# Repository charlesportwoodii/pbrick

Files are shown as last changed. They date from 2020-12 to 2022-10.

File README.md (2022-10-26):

<div align="center">
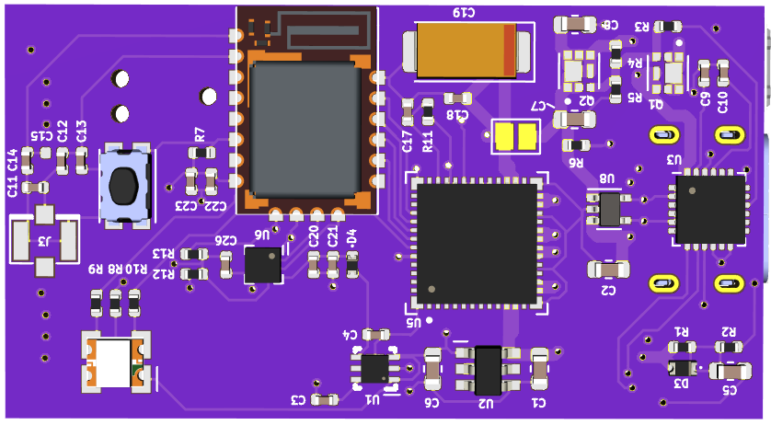
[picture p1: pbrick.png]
  

  <h1>PBRICK</h1>

  <p>
    <strong>A USB-C PD powered, Bluetooh controlled motor driver and IO software and hardware.</strong>
  </p>
  <hr />
</div>

## About
PBrick is a personal project born out of a desire to learn Kicad, and develop embedded software, learn USB-C PD, and create a full end-to-end software solutions. I currently use pbrick to power a few custom toys, and other things that require motor driver for toys and gadgets.

While I won't call this "battle-tested" hardware and software, I have successfully manufactured and used it for over a year now without problem or incident.

This board has been in various stages of development since 2018, and has been significantly impacted by the semi-conductor supply chain.

## Features

- Dual motor driver for powering two separate motors independently, up to 20V5A (100W of power), and 12V3A per rail
- Dual motor driver ouputs on rear of board with input power output rails + GND
- USB-C Power Delivery (PD) input
- Configurable JST-2 pin connector for either PD output when using USB-C PD, or direct power input with backfeed protection
    (You may power the board either by USB-PD or by this PIN)
- i2c output on rear of board for running and powering additional accessories
- Programmable LED Status light
- Single button with double tap to reset functionality available in the [Kaidyth Bootloader](https://github.com/kaidyth/nrf52_bootloader)
- Accelerometer for rollover detection
- 4 Layer board with dedicated GND layer

## Board Pictures

<div align="center">
  
  

  <br />
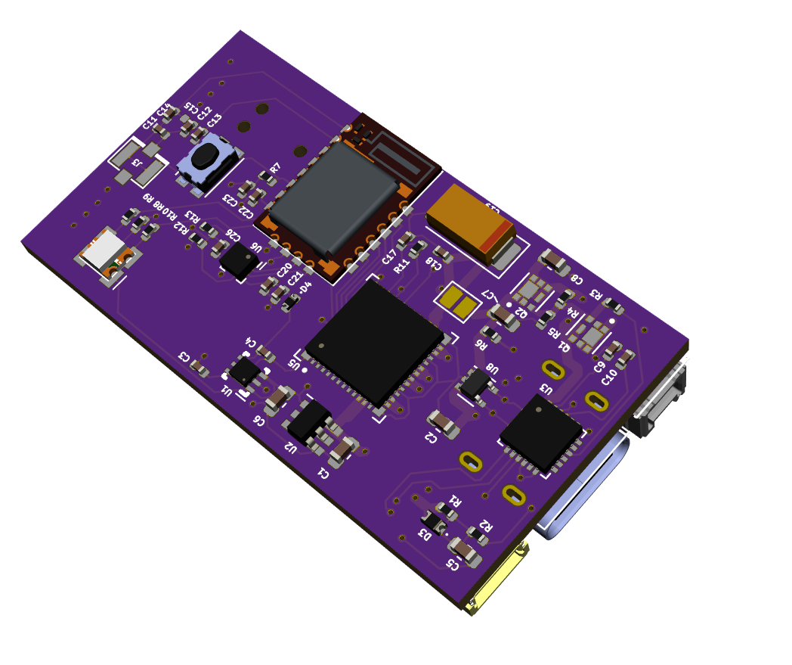
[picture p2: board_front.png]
  

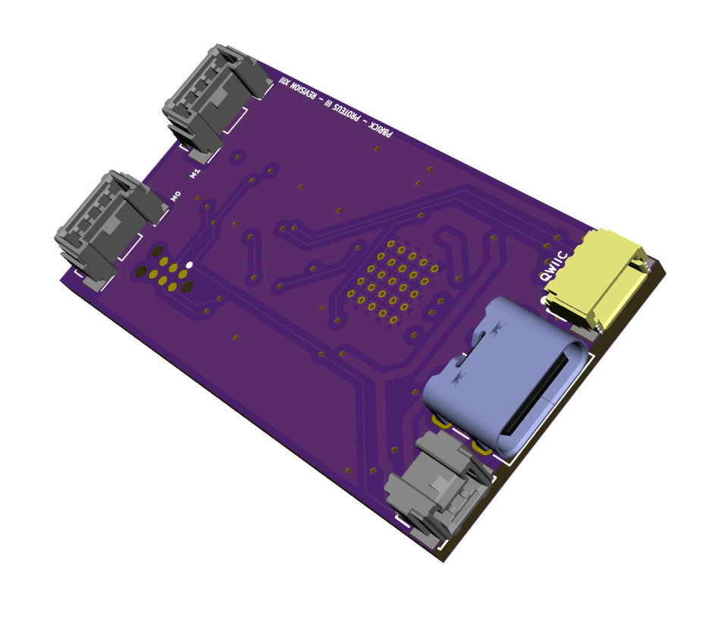
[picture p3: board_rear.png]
  
</div>

## Schematic
The current schematic is available at https://github.com/charlesportwoodii/pbrick/blob/TB67H420FTG-24MM-C-a/board/schematic.pdf.

## Revisions
There are a number of revisions to the board. The active branch is `TB67H420FTG-24MM-C-a` .

## Production Notes
COVID-19 continues to cause part shortages, and I cannot currently provide any guarantees or alternative parts. Here's a few notes from my production of this revision of the board should you choose to make it yourself.

- I'd recommend OshPark + Osh Stencils to create the board and the stencil. Use a heat gun for soldering, then hand solder the external connections.
- After soldering and verifying all the components, I strongly recommend super-gluing the USB-C port directly to the board at the connection points. It's not difficult to break the connection by accident with just solder.
- You may ommit the accelerometer, and any i2c components depending upon available.
- The board should stay fairly cool even when running multiple motors on the same channel. If the board starts to rapidly heat up I am almost guarantee you have a bridge on the motor pins.
- I strongly recommend adding additional solder to JP1 bridge that connects VSS to VDD (see schematic). Be generous and liberal as this is the main power bus. The Jumper is used here as there is an alternative configuration where it can be cut and the board can be powered from one of the outputs but that's not supported yet so don't do it.
- Despite the abundance of USB-C PD devices on Amazon _a lot_ of them don't actually support USB-C PD (most really only provide proprietary protocols). The best I've found is [XCentz 5000mAh Charger](https://www.amazon.com/gp/product/B07LB18B73/ref=ppx_yo_dt_b_search_asin_title?ie=UTF8&psc=1) but again, COVID has made stock + availability intermittent.
- You'll probably want a very short USB-C PD cable. The shortest I've found is: https://www.amazon.com/gp/product/B08L8Z7YJ8/ref=ppx_yo_dt_b_search_asin_title?ie=UTF8&psc=1.
- Q1 and Q2 will protect any backfeed current from J5 _however_ if you're going to power the board over J5, I would completely omit the USB-C PD section of the board, and cut JP1 to prevent power flowing to that entire section of the board.

## Functionality Notes

- Currently there's no software to measure or control the accelerometer due to stock and availability. I simply have never been able to source the part. The intent with the accelerometer is to provide "rollover" detection in the event the object/toy falls off the track or rolls over or experiences a significant G force event so that the power to the motors can be either momentarily or permanently cut.
- You can use the nRF Connect app to send the payload to the Motor service. The payload is a 3 byte serial, <MOTOR><SPEED><DIRECTION>
Motor selection being 00, and 01 for the respective board MX, the "speed" value being the PWM speed from 00-64 (anything greater than 64 is considered 64), and the direction parameter which will set the motor direction. There's a special mode 0x02 and 0x03 which will cause both motors to run at the same speed + PWM either in the same, or in opposite directions if you need to syncronize them. Feel free to play around with the inputs.
- Flash the board with both the Kaidyth Bootloader, and a compiled version so that you have full DFU support. Using other bootloaders will result in error.

## License

PBRICK is currently source-available. For non-commercial scientific research, non-commercial education, or non-commercial artistic projects, PBRICK is available under the BSD-3 Clause license. No commercial license is permitted whatsoever.

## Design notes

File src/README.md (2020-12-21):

# PBrick



A firmware package for Nordic nRF52 chipset made for powering legos, models, and other gadgets with motor, lighting, and other controls over Bluetooth low energy.

## Documentation

Complete documentation for board support, adding new boards, compiling, and more is provided in the [Wiki](https://github.com/charlesportwoodii/pbrick/wiki).

## Installing

1. Burn the [Kaidyth nRF52 Bootloader](https://github.com/charlesportwoodii/kaidyth_nrf52_bootloader/releases) using `nrfjprog`. Grab a hex/zip for your supported board.

    ```
    nrfjprog -f nrf52 --erase
    nrfjprog -f nrf52 --program nrf52840_xxaa_s140_<board>.hex

    # For PCA10059 reset UICR before resetting
    nrfjprog --memwr 0x10001304 --val 0xFFFFFFFD

    nrfjprog -f nf52 --reset
    ```

    > You'll need a Segger J-LINK in order to flash the bootloader with the Adafruit bootloader for the first time. Once the Adafruit bootloader is flashed, you can use `adafruit-nrfutil` to update the bootloader. Adafruit sells a [J-Link EDU Mini](https://www.adafruit.com/product/3571) for $19.99 USD if you need a cheap J-Link

2. Flash the PBrick hex to your board using either nRF Connect or `nrfutil`.

    If you're making changes, run `make <board>` to build your custom solution.

    > You can download pre-compiled binaries from the [releases](https://github.com/charlesportwoodii/pbrick/releases) page if you're just looking to use PBrick.

## Building

Take a look at the [Getting Started](https://github.com/charlesportwoodii/pbrick/wiki/Getting-Started) page for more information on the dependencies needed.

With your dependencies installed you can compile the project for supported boards by running `make`

```
make <board>
```

> Run `make` without a board specified to see a list of supported boards.
> You can also run `make all` to build all boards.

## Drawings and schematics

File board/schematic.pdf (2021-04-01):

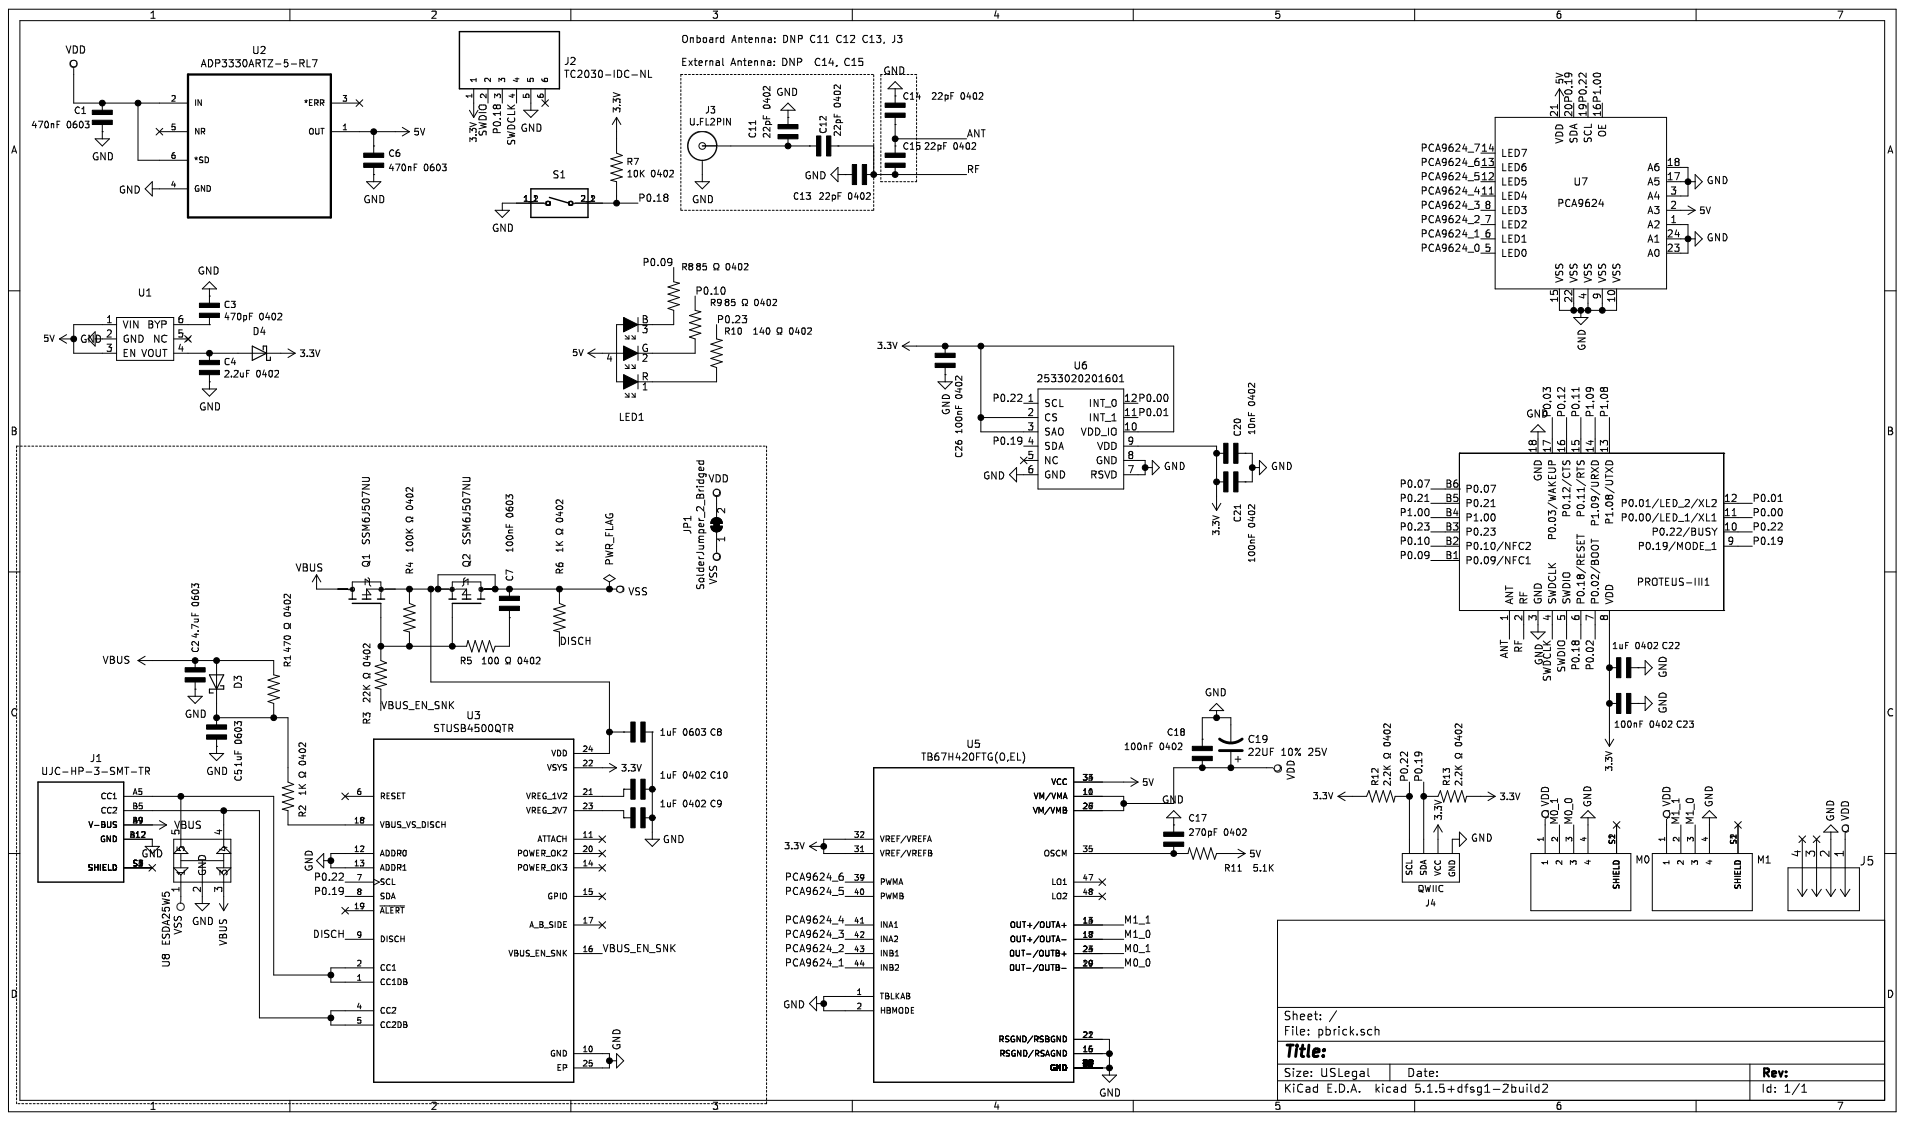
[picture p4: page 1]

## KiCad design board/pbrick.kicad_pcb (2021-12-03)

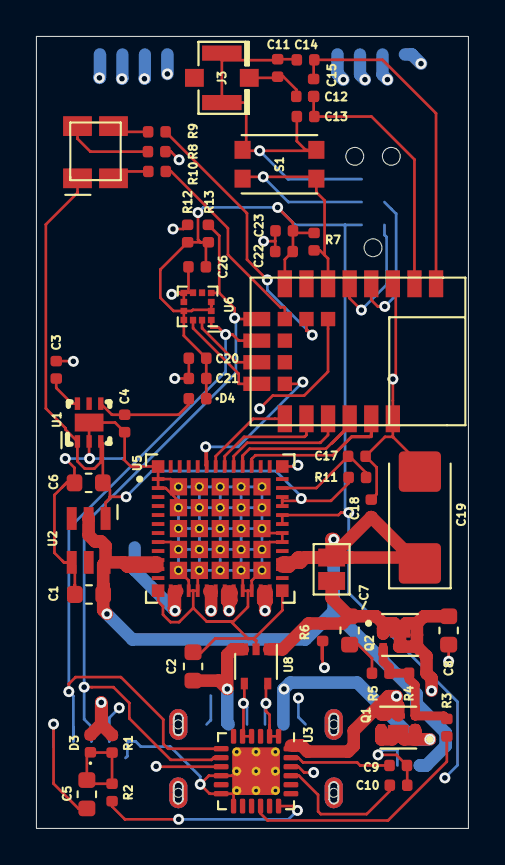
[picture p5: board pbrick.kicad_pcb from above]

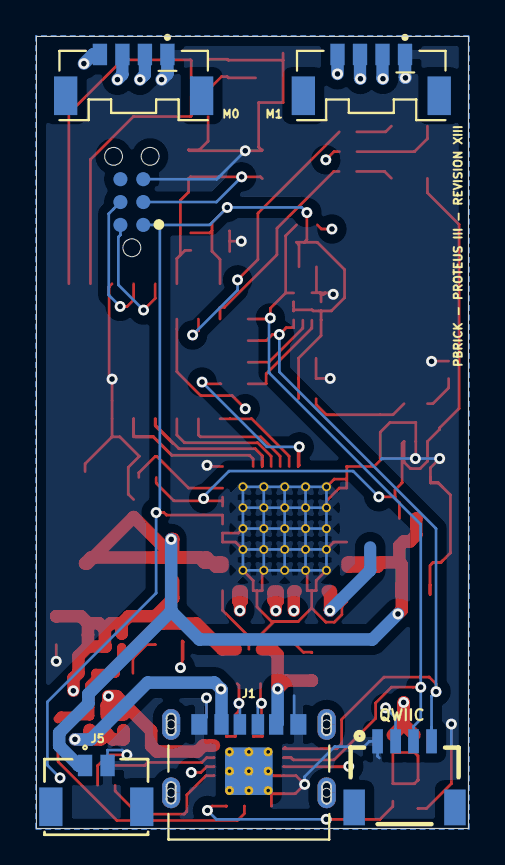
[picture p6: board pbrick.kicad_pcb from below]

Board: 4 copper layers, 24.0 x 44.0 mm, 57 parts (6 on the bottom side), 45 nets.

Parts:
C1, C6: 470nF 0603; C_0603_1608Metric
C2: 4.7uF 0603; C_0603_1608Metric
C3: 470pF 0402; C_0402_1005Metric
C4: 2.2uF 0402; C_0402_1005Metric
C5, C8: 1uF 0603; C_0603_1608Metric
C7: 100nF 0603; C_0603_1608Metric
C9, C10, C22: 1uF 0402; C_0402_1005Metric
C11, C12, C13, C14, C15: 22pF 0402; C_0402_1005Metric
C17: 270pF 0402; C_0402_1005Metric
C18, C20, C21, C23, C26: 100nF 0402; C_0402_1005Metric
C19: 22UF 10% 25V; CP_EIA-6032-15_Kemet-U_Pad2.25x2.35mm_HandSolder
D3, D4: D_Schottky; D_0402_1005Metric
J1: UJC-HP-3-SMT-TR; CUI_UJC-HP-3-SMT-TR
J2: TC2030-IDC-NL; TAG_TC2030-IDC-NL
J3: U.FL2PIN; U.FL
J4: QWIIC; 1X04_1MM_RA
J5: 5055670271
JP1: SolderJumper_2_Bridged; SolderJumper-2_P1.3mm_Open_Pad1.0x1.5mm
LED1: 150121M153000
M0, M1: 5055680471; MOLEX_5055680471
PROTEUS-III1: PROTEUS-III; WIRL-BLTE_Proteus-III
Q1, Q2: SSM6J507NU; TRANS_SSM6J507NU,LF
R1: 470 Ω 0402; R_0402_1005Metric
R2, R6: 1K Ω 0402; R_0402_1005Metric
R3: 22K Ω 0402; R_0402_1005Metric
R4: 100K Ω 0402; R_0402_1005Metric
R5: 100 Ω 0402; R_0402_1005Metric
R7: 10K 0402; R_0402_1005Metric
R8, R9: 85 Ω 0402; R_0402_1005Metric
R10: 140 Ω 0402; R_0402_1005Metric
R11: 5.1K; R_0402_1005Metric
R12, R13: 2.2K Ω 0402; R_0402_1005Metric
S1: KMR621NGLFS; SW_KMR621NGLFS
U1: MIC5219-3.3YML-TR; QFN6_THERMAL_PAD
U2: ADP3330ARTZ-5-RL7; SOT95P280X145-6N
U3: STUSB4500QTR; QFN-24-1EP_4x4mm_P0.5mm_EP2.65x2.65mm_ThermalVias
U5: TB67H420FTG(O,EL); IC_TB67H420FTG(O,EL)
U6: 2533020201601; LGA-12_2x2mm_P0.5mm
U8: ESDA25W5; SOT-353_SC-70-5

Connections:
3.3V: C20.2, C21.2, C22.1, C23.1, C26.2, D4.1, J2.1, J4.2, PROTEUS-III1.8, R7.1, R12.1, R13.2, U3.22, U5.31, U5.32, U6.2, U6.3, U6.9, U6.10
5V: C6.1, LED1.4, R11.1, U1.1, U1.3, U2.1, U5.33, U5.34
/ANT: C14.2, C15.1, PROTEUS-III1.1
/DISCH: R6.2, U3.9
/M0_0: M0.3, U5.19, U5.20
/M0_1: M0.2, U5.23, U5.24
/M1_0: M1.2, U5.17, U5.18
/M1_1: M1.3, U5.13, U5.14
/P0.00: PROTEUS-III1.11, U6.12
/P0.01: PROTEUS-III1.12, U6.11
/P0.03: PROTEUS-III1.17, U5.39
/P0.07: PROTEUS-III1.B6, U5.44
/P0.09: PROTEUS-III1.B1, R8.2
/P0.10: PROTEUS-III1.B2, R9.2
/P0.11: PROTEUS-III1.15, U5.41
/P0.12: PROTEUS-III1.16, U5.40
/P0.18: J2.3, PROTEUS-III1.6, R7.2, S1.2_1, S1.2_2
/P0.19: J4.3, PROTEUS-III1.9, R13.1, U3.8, U6.4
/P0.22: J4.4, PROTEUS-III1.10, R12.2, U3.7, U6.1
/P0.23: PROTEUS-III1.B3, R10.2
/P1.08: PROTEUS-III1.13, U5.43
/P1.09: PROTEUS-III1.14, U5.42
/RF: C12.1, C13.1, C15.2, PROTEUS-III1.2
/SWDCLK: J2.4, PROTEUS-III1.4
/SWDIO: J2.2, PROTEUS-III1.5
/VBUS_EN_SNK: R3.2, U3.16
GND: C1.2, C2.2, C3.1, C4.2, C5.2, C6.2, C8.1, C9.1, C10.1, C11.1, C13.2, C14.1, C17.1, C18.1, C19.2, C20.1, C21.1, C22.2, C23.2, C26.1, J1.A12, J1.B12, J2.5, J3.1, J3.2, J4.1, J5.2, M0.1, M1.1, PROTEUS-III1.3, PROTEUS-III1.18, S1.1_1, S1.1_2, U1.2, U2.4, U3.10, U3.12, U3.13, U3.25, U5.1, U5.2, U5.8, U5.15, U5.16, U5.21, U5.22, U5.29, U5.30, U5.49, U5.50, U5.51, U5.52, U5.53, U5.54, U5.55, U5.56, U5.57, U5.58, U5.59, U5.60, U5.61, U5.62, U5.63, U5.64, U5.65, U5.66, U5.67, U5.68, U5.69, U5.70, U5.71, U5.72, U5.73, U5.74, U5.75, U5.76, U5.77, U5.78, U5.79, U5.80, U5.81, U5.82, U5.83, U5.84, U5.85, U5.86, U5.87, U5.88, U5.89, U5.90, U5.91, U5.92, U5.93, U5.94, U5.95, U5.96, U5.97, U5.98, U5.G1, U5.G2, U5.G3, U5.G4, U6.6, U6.7, U6.8, U8.2
unnamed: C3.2, U1.6
unnamed: C4.1, D4.2, U1.4
unnamed: C5.1, D3.1, R1.1, R2.1
unnamed: C7.2, R5.1
unnamed: C9.2, U3.23
unnamed: C10.2, U3.21
unnamed: C11.2, C12.2, J3.FEED
unnamed: C17.2, R11.2, U5.35
unnamed: J1.A5, U3.1, U3.2, U8.5
unnamed: J1.B5, U3.4, U3.5, U8.4
unnamed: LED1.1, R10.1
unnamed: LED1.2, R9.1
unnamed: LED1.3, R8.1
unnamed: Q1.3, Q2.3, R3.1, R4.2, R5.2
unnamed: R2.2, U3.18
VBUS: C2.1, D3.2, J1.A9, J1.B9, Q1.1, Q1.2, Q1.5, Q1.6, Q1.7, R1.2, U8.3
VDD: C1.1, C18.2, C19.1, J5.1, JP1.2, M0.4, M1.4, U2.2, U2.6, U5.10, U5.11, U5.26, U5.27
VSS: C7.1, C8.2, JP1.1, Q1.4, Q1.8, Q2.1, Q2.2, Q2.4, Q2.5, Q2.6, Q2.7, Q2.8, R4.1, R6.1, U3.24, U8.1

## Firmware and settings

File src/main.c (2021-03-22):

/**
 * Copyright (c) 2014 - 2019, Nordic Semiconductor ASA
 *
 * All rights reserved.
 *
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
 * 3. Neither the name of Nordic Semiconductor ASA nor the names of its
 *    contributors may be used to endorse or promote products derived from this
 *    software without specific prior written permission.
 *
 * 4. This software, with or without modification, must only be used with a
 *    Nordic Semiconductor ASA integrated circuit.
 *
 * 5. Any software provided in binary form under this license must not be reverse
 *    engineered, decompiled, modified and/or disassembled.
 *
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
 */
/** @example examples/ble_peripheral/ble_app_buttonless_dfu
 *
 * @brief Secure DFU Buttonless Service Application main file.
 *
 * This file contains the source code for a sample application using the proprietary
 * Secure DFU Buttonless Service. This is a template application that can be modified
 * to your needs. To extend the functionality of this application, please find
 * locations where the comment "// YOUR_JOB:" is present and read the comments.
 */

#include <stdbool.h>
#include <stdint.h>
#include <string.h>

#include "nrf_dfu_ble_svci_bond_sharing.h"
#include "nrf_svci_async_function.h"
#include "nrf_svci_async_handler.h"

#include "nordic_common.h"
#include "nrf.h"
#include "nrf_delay.h"
#include "app_error.h"
#include "ble.h"
#include "ble_hci.h"
#include "ble_srv_common.h"
#include "ble_advdata.h"
#include "ble_advertising.h"
#include "ble_conn_params.h"
#include "nrf_sdh.h"
#include "nrf_sdh_soc.h"
#include "nrf_sdh_ble.h"
#include "app_timer.h"
#include "peer_manager.h"
#include "peer_manager_handler.h"
#include "bsp_btn_ble.h"
#include "ble_hci.h"
#include "ble_advdata.h"
#include "ble_advertising.h"
#include "ble_conn_state.h"
#include "ble_dfu.h"
#include "nrf_ble_gatt.h"
#include "nrf_ble_qwr.h"
#include "fds.h"
#include "nrf_pwr_mgmt.h"
#include "nrf_drv_clock.h"
#include "nrf_power.h"
#include "nrf_log.h"
#include "nrf_log_ctrl.h"
#include "nrf_log_default_backends.h"
#include "nrf_bootloader_info.h"
#include "nrf_drv_twi.h"

#include "pbrick_board.h"
#include "ble_pbrick.h"
#include "pbrick_twi.h"
#include "STUSB4500.h"
#include "nrf_drv_twi.h"

#define DEVICE_NAME                     "PBRICK"                                    /**< Name of device. Will be included in the advertising data. */
#define MANUFACTURER_NAME               "NordicSemiconductor"                       /**< Manufacturer. Will be passed to Device Information Service. */
#define APP_ADV_INTERVAL                300                                         /**< The advertising interval (in units of 0.625 ms. This value corresponds to 187.5 ms). */
#define APP_ADV_DURATION                18000                                       /**< The advertising duration (180 seconds) in units of 10 milliseconds. */

#define APP_BLE_OBSERVER_PRIO           3                                           /**< Application's BLE observer priority. You shouldn't need to modify this value. */
#define APP_BLE_CONN_CFG_TAG            1                                           /**< A tag identifying the SoftDevice BLE configuration. */

#define MIN_CONN_INTERVAL               MSEC_TO_UNITS(100, UNIT_1_25_MS)            /**< Minimum acceptable connection interval (0.1 seconds). */
#define MAX_CONN_INTERVAL               MSEC_TO_UNITS(200, UNIT_1_25_MS)            /**< Maximum acceptable connection interval (0.2 second). */
#define SLAVE_LATENCY                   0                                           /**< Slave latency. */
#define CONN_SUP_TIMEOUT                MSEC_TO_UNITS(4000, UNIT_10_MS)             /**< Connection supervisory timeout (4 seconds). */

#define FIRST_CONN_PARAMS_UPDATE_DELAY  APP_TIMER_TICKS(5000)                       /**< Time from initiating event (connect or start of notification) to first time sd_ble_gap_conn_param_update is called (5 seconds). */
#define NEXT_CONN_PARAMS_UPDATE_DELAY   APP_TIMER_TICKS(30000)                      /**< Time between each call to sd_ble_gap_conn_param_update after the first call (30 seconds). */
#define MAX_CONN_PARAMS_UPDATE_COUNT    3                                           /**< Number of attempts before giving up the connection parameter negotiation. */

#define SEC_PARAM_BOND                  1                                           /**< Perform bonding. */
#define SEC_PARAM_MITM                  0                                           /**< Man In The Middle protection not required. */
#define SEC_PARAM_LESC                  0                                           /**< LE Secure Connections not enabled. */
#define SEC_PARAM_KEYPRESS              0                                           /**< Keypress notifications not enabled. */
#define SEC_PARAM_IO_CAPABILITIES       BLE_GAP_IO_CAPS_NONE                        /**< No I/O capabilities. */
#define SEC_PARAM_OOB                   0                                           /**< Out Of Band data not available. */
#define SEC_PARAM_MIN_KEY_SIZE          7                                           /**< Minimum encryption key size. */
#define SEC_PARAM_MAX_KEY_SIZE          16                                          /**< Maximum encryption key size. */

#define DEAD_BEEF                       0xDEADBEEF                                  /**< Value used as error code on stack dump, can be used to identify stack location on stack unwind. */

BLE_PBRICK_DEF(m_pbrick);

NRF_BLE_GATT_DEF(m_gatt);                                                           /**< GATT module instance. */
NRF_BLE_QWR_DEF(m_qwr);                                                             /**< Context for the Queued Write module.*/
BLE_ADVERTISING_DEF(m_advertising);                                                 /**< Advertising module instance. */

static uint16_t m_conn_handle = BLE_CONN_HANDLE_INVALID;                            /**< Handle of the current connection. */
static void advertising_start(bool erase_bonds);                                    /**< Forward declaration of advertising start function */

// YOUR_JOB: Use UUIDs for service(s) used in your application.
static ble_uuid_t m_adv_uuids[] = {
    {PBRICK_SERIVCE_UUID, BLE_UUID_TYPE_VENDOR_BEGIN}
};

void HardFault_Handler(void)
{
    uint32_t *sp = (uint32_t *) __get_MSP(); // Get stack pointer
    uint32_t ia = sp[12]; // Get instruction address from stack

    printf("Hard Fault at address: 0x%08x\r\n", (unsigned int)ia);
    while(1)
        ;
}

/**@brief Handler for shutdown preparation.
 *
 * @details During shutdown procedures, this function will be called at a 1 second interval
 *          untill the function returns true. When the function returns true, it means that the
 *          app is ready to reset to DFU mode.
 *
 * @param[in]   event   Power manager event.
 *
 * @retval  True if shutdown is allowed by this power manager handler, otherwise false.
 */
static bool app_shutdown_handler(nrf_pwr_mgmt_evt_t event)
{
    switch (event)
    {
        case NRF_PWR_MGMT_EVT_PREPARE_DFU:
            NRF_LOG_INFO("Power management wants to reset to DFU mode.");
            ble_pbrick_shutdown();
            break;

        default:
            // YOUR_JOB: Implement any of the other events available from the power management module:
            //      -NRF_PWR_MGMT_EVT_PREPARE_SYSOFF
            //      -NRF_PWR_MGMT_EVT_PREPARE_WAKEUP
            //      -NRF_PWR_MGMT_EVT_PREPARE_RESET
            return true;
    }

    NRF_LOG_INFO("Power management allowed to reset to DFU mode.");
    return true;
}

//lint -esym(528, m_app_shutdown_handler)
/**@brief Register application shutdown handler with priority 0.
 */
NRF_PWR_MGMT_HANDLER_REGISTER(app_shutdown_handler, 0);


static void buttonless_dfu_sdh_state_observer(nrf_sdh_state_evt_t state, void * p_context)
{
    if (state == NRF_SDH_EVT_STATE_DISABLED)
    {
        // Softdevice was disabled before going into reset. Inform bootloader to skip CRC on next boot.
        nrf_power_gpregret2_set(BOOTLOADER_DFU_SKIP_CRC);

        //Go to system off.
        nrf_pwr_mgmt_shutdown(NRF_PWR_MGMT_SHUTDOWN_GOTO_SYSOFF);
    }
}

/* nrf_sdh state observer. */
NRF_SDH_STATE_OBSERVER(m_buttonless_dfu_state_obs, 0) =
{
    .handler = buttonless_dfu_sdh_state_observer,
};


static void advertising_config_get(ble_adv_modes_config_t * p_config)
{
    memset(p_config, 0, sizeof(ble_adv_modes_config_t));

    p_config->ble_adv_fast_enabled  = true;
    p_config->ble_adv_fast_interval = APP_ADV_INTERVAL;
    p_config->ble_adv_fast_timeout  = APP_ADV_DURATION;
}


static void disconnect(uint16_t conn_handle, void * p_context)
{
    UNUSED_PARAMETER(p_context);

    ret_code_t err_code = sd_ble_gap_disconnect(conn_handle, BLE_HCI_REMOTE_USER_TERMINATED_CONNECTION);
    if (err_code != NRF_SUCCESS)
    {
        NRF_LOG_WARNING("Failed to disconnect connection. Connection handle: %d Error: %d", conn_handle, err_code);
    }
    else
    {
        NRF_LOG_DEBUG("Disconnected connection handle %d", conn_handle);
    }
}


// YOUR_JOB: Update this code if you want to do anything given a DFU event (optional).
/**@brief Function for handling dfu events from the Buttonless Secure DFU service
 *
 * @param[in]   event   Event from the Buttonless Secure DFU service.
 */
static void ble_dfu_evt_handler(ble_dfu_buttonless_evt_type_t event)
{
    switch (event)
    {
        case BLE_DFU_EVT_BOOTLOADER_ENTER_PREPARE:
        {
            NRF_LOG_INFO("Device is preparing to enter bootloader mode.");

            // Prevent device from advertising on disconnect.
            ble_adv_modes_config_t config;
            advertising_config_get(&config);
            config.ble_adv_on_disconnect_disabled = true;
            ble_advertising_modes_config_set(&m_advertising, &config);

            // Disconnect all other bonded devices that currently are connected.
            // This is required to receive a service changed indication
            // on bootup after a successful (or aborted) Device Firmware Update.
            uint32_t conn_count = ble_conn_state_for_each_connected(disconnect, NULL);
            NRF_LOG_INFO("Disconnected %d links.", conn_count);
            break;
        }

        case BLE_DFU_EVT_BOOTLOADER_ENTER:
            // YOUR_JOB: Write app-specific unwritten data to FLASH, control finalization of this
            //           by delaying reset by reporting false in app_shutdown_handler
            NRF_LOG_INFO("Device will enter bootloader mode.");
            break;

        case BLE_DFU_EVT_BOOTLOADER_ENTER_FAILED:
            NRF_LOG_ERROR("Request to enter bootloader mode failed asynchroneously.");
            // YOUR_JOB: Take corrective measures to resolve the issue
            //           like calling APP_ERROR_CHECK to reset the device.
            break;

        case BLE_DFU_EVT_RESPONSE_SEND_ERROR:
            NRF_LOG_ERROR("Request to send a response to client failed.");
            // YOUR_JOB: Take corrective measures to resolve the issue
            //           like calling APP_ERROR_CHECK to reset the device.
            APP_ERROR_CHECK(false);
            break;

        default:
            NRF_LOG_ERROR("Unknown event from ble_dfu_buttonless.");
            break;
    }
}


/**@brief Callback function for asserts in the SoftDevice.
 *
 * @details This function will be called in case of an assert in the SoftDevice.
 *
 * @warning This handler is an example only and does not fit a final product. You need to analyze
 *          how your product is supposed to react in case of Assert.
 * @warning On assert from the SoftDevice, the system can only recover on reset.
 *
 * @param[in] line_num   Line number of the failing ASSERT call.
 * @param[in] file_name  File name of the failing ASSERT call.
 */
void assert_nrf_callback(uint16_t line_num, const uint8_t * p_file_name)
{
    app_error_handler(DEAD_BEEF, line_num, p_file_name);
}


/**@brief Function for handling Peer Manager events.
 *
 * @param[in] p_evt  Peer Manager event.
 */
static void pm_evt_handler(pm_evt_t const * p_evt)
{
    pm_handler_on_pm_evt(p_evt);
    pm_handler_flash_clean(p_evt);
}


/**@brief Function for the Timer initialization.
 *
 * @details Initializes the timer module. This creates and starts application timers.
 */
static void timers_init(void)
{

    // Initialize timer module.
    uint32_t err_code = app_timer_init();
    APP_ERROR_CHECK(err_code);

    // Create timers.

    /* YOUR_JOB: Create any timers to be used by the application.
                 Below is an example of how to create a timer.
                 For every new timer needed, increase the value of the macro APP_TIMER_MAX_TIMERS by
                 one.
       uint32_t err_code;
       err_code = app_timer_create(&m_app_timer_id, APP_TIMER_MODE_REPEATED, timer_timeout_handler);
       APP_ERROR_CHECK(err_code); */
}


/**@brief Function for the GAP initialization.
 *
 * @details This function sets up all the necessary GAP (Generic Access Profile) parameters of the
 *          device including the device name, appearance, and the preferred connection parameters.
 */
static void gap_params_init(void)
{
    uint32_t                err_code;
    ble_gap_conn_params_t   gap_conn_params;
    ble_gap_conn_sec_mode_t sec_mode;

    BLE_GAP_CONN_SEC_MODE_SET_OPEN(&sec_mode);

    err_code = sd_ble_gap_device_name_set(&sec_mode,
                                          (const uint8_t *)DEVICE_NAME,
                                          strlen(DEVICE_NAME));
    APP_ERROR_CHECK(err_code);

    /* YOUR_JOB: Use an appearance value matching the application's use case.
       err_code = sd_ble_gap_appearance_set(BLE_APPEARANCE_);
       APP_ERROR_CHECK(err_code); */

    memset(&gap_conn_params, 0, sizeof(gap_conn_params));

    gap_conn_params.min_conn_interval = MIN_CONN_INTERVAL;
    gap_conn_params.max_conn_interval = MAX_CONN_INTERVAL;
    gap_conn_params.slave_latency     = SLAVE_LATENCY;
    gap_conn_params.conn_sup_timeout  = CONN_SUP_TIMEOUT;

    err_code = sd_ble_gap_ppcp_set(&gap_conn_params);
    APP_ERROR_CHECK(err_code);
}


/**@brief Function for handling Queued Write Module errors.
 *
 * @details A pointer to this function will be passed to each service which may need to inform the
 *          application about an error.
 *
 * @param[in]   nrf_error   Error code containing information about what went wrong.
 */
static void nrf_qwr_error_handler(uint32_t nrf_error)
{
    APP_ERROR_HANDLER(nrf_error);
}


/**@brief Function for handling the YYY Service events.
 * YOUR_JOB implement a service handler function depending on the event the service you are using can generate
 *
 * @details This function will be called for all YY Service events which are passed to
 *          the application.
 *
 * @param[in]   p_yy_service   YY Service structure.
 * @param[in]   p_evt          Event received from the YY Service.
 *
 *
   static void on_yys_evt(ble_yy_service_t     * p_yy_service,
                          ble_yy_service_evt_t * p_evt)
   {
    switch (p_evt->evt_type)
    {
        case BLE_YY_NAME_EVT_WRITE:
            APPL_LOG("[APPL]: charact written with value %s. ", p_evt->params.char_xx.value.p_str);
            break;

        default:
            // No implementation needed.
            break;
    }
   }*/


/**@brief Function for initializing services that will be used by the application.
 */
static void services_init(void)
{
    uint32_t                  err_code;
    nrf_ble_qwr_init_t        qwr_init  = {0};
    ble_dfu_buttonless_init_t dfus_init = {0};
    ble_pbrick_init_t  pbrick_init;

    // Initialize Queued Write Module.
    qwr_init.error_handler = nrf_qwr_error_handler;

    err_code = nrf_ble_qwr_init(&m_qwr, &qwr_init);
    APP_ERROR_CHECK(err_code);

    dfus_init.evt_handler = ble_dfu_evt_handler;

    err_code = ble_dfu_buttonless_init(&dfus_init);
    APP_ERROR_CHECK(err_code);

    memset(&pbrick_init, 0, sizeof(pbrick_init));

    BLE_GAP_CONN_SEC_MODE_SET_OPEN(&pbrick_init.motor_char_attr_md.read_perm);
    BLE_GAP_CONN_SEC_MODE_SET_OPEN(&pbrick_init.motor_char_attr_md.write_perm);

    err_code = ble_pbrick_init(&m_pbrick, &pbrick_init);
    APP_ERROR_CHECK(err_code);
}


/**@brief Function for handling the Connection Parameters Module.
 *
 * @details This function will be called for all events in the Connection Parameters Module which
 *          are passed to the application.
 *          @note All this function does is to disconnect. This could have been done by simply
 *                setting the disconnect_on_fail config parameter, but instead we use the event
 *                handler mechanism to demonstrate its use.
 *
 * @param[in] p_evt  Event received from the Connection Parameters Module.
 */
static void on_conn_params_evt(ble_conn_params_evt_t * p_evt)
{
    uint32_t err_code;

    if (p_evt->evt_type == BLE_CONN_PARAMS_EVT_FAILED)
    {
        err_code = sd_ble_gap_disconnect(m_conn_handle, BLE_HCI_CONN_INTERVAL_UNACCEPTABLE);
        APP_ERROR_CHECK(err_code);
    }
}


/**@brief Function for handling a Connection Parameters error.
 *
 * @param[in] nrf_error  Error code containing information about what went wrong.
 */
static void conn_params_error_handler(uint32_t nrf_error)
{
    APP_ERROR_HANDLER(nrf_error);
}


/**@brief Function for initializing the Connection Parameters module.
 */
static void conn_params_init(void)
{
    uint32_t               err_code;
    ble_conn_params_init_t cp_init;

    memset(&cp_init, 0, sizeof(cp_init));

    cp_init.p_conn_params                  = NULL;
    cp_init.first_conn_params_update_delay = FIRST_CONN_PARAMS_UPDATE_DELAY;
    cp_init.next_conn_params_update_delay  = NEXT_CONN_PARAMS_UPDATE_DELAY;
    cp_init.max_conn_params_update_count   = MAX_CONN_PARAMS_UPDATE_COUNT;
    cp_init.start_on_notify_cccd_handle    = BLE_GATT_HANDLE_INVALID;
    cp_init.disconnect_on_fail             = false;
    cp_init.evt_handler                    = on_conn_params_evt;
    cp_init.error_handler                  = conn_params_error_handler;

    err_code = ble_conn_params_init(&cp_init);
    APP_ERROR_CHECK(err_code);
}


/**@brief Function for starting timers.
 */
static void application_timers_start(void)
{
    /* YOUR_JOB: Start your timers. below is an example of how to start a timer.
       uint32_t err_code;
       err_code = app_timer_start(m_app_timer_id, TIMER_INTERVAL, NULL);
       APP_ERROR_CHECK(err_code); */
}


/**@brief Function for putting the chip into sleep mode.
 *
 * @note This function will not return.
 */
static void sleep_mode_enter(void)
{
    uint32_t err_code = bsp_indication_set(BSP_INDICATE_IDLE);

    APP_ERROR_CHECK(err_code);

    // Prepare wakeup buttons.
    err_code = bsp_btn_ble_sleep_mode_prepare();
    APP_ERROR_CHECK(err_code);

    //Disable SoftDevice. It is required to be able to write to GPREGRET2 register (SoftDevice API blocks it).
    //GPREGRET2 register holds the information about skipping CRC check on next boot.
    err_code = nrf_sdh_disable_request();
    APP_ERROR_CHECK(err_code);
}


/**@brief Function for handling advertising events.
 *
 * @details This function will be called for advertising events which are passed to the application.
 *
 * @param[in] ble_adv_evt  Advertising event.
 */
static void on_adv_evt(ble_adv_evt_t ble_adv_evt)
{
    uint32_t err_code;

    switch (ble_adv_evt)
    {
        case BLE_ADV_EVT_FAST:
            err_code = bsp_indication_set(BSP_INDICATE_ADVERTISING);
            APP_ERROR_CHECK(err_code);
            break;

        case BLE_ADV_EVT_IDLE:
            sleep_mode_enter();
            break;

        default:
            break;
    }
}
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
int main(void)
{
    bool erase_bonds;
    ret_code_t err_code;

    log_init();
    pd_init();

    // Initialize the async SVCI interface to bootloader before any interrupts are enabled.
    err_code = ble_dfu_buttonless_async_svci_init();
    APP_ERROR_CHECK(err_code);

    timers_init();
    buttons_leds_init(&erase_bonds);
    power_management_init();
    ble_stack_init();
    gap_params_init();
    gatt_init();
    services_init();
    advertising_init();
    conn_params_init();
    peer_manager_init();

    // Start execution.
    application_timers_start();
    advertising_start(erase_bonds);

    // Enter main loop.
    for (;;) {
        idle_state_handle();
    }
}

/**
 * @}
 */

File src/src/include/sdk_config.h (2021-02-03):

/**
 * Copyright (c) 2017 - 2019, Nordic Semiconductor ASA
 *
 * All rights reserved.
 *
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
 * 3. Neither the name of Nordic Semiconductor ASA nor the names of its
 *    contributors may be used to endorse or promote products derived from this
 *    software without specific prior written permission.
 *
 * 4. This software, with or without modification, must only be used with a
 *    Nordic Semiconductor ASA integrated circuit.
 *
 * 5. Any software provided in binary form under this license must not be reverse
 *    engineered, decompiled, modified and/or disassembled.
 *
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
 */



#ifndef SDK_CONFIG_H
#define SDK_CONFIG_H
#include "app_config.h"
// <h> Board Support

//==========================================================
// <q> BSP_BTN_BLE_ENABLED  - bsp_btn_ble - Button Control for BLE


#ifndef BSP_BTN_BLE_ENABLED
#define BSP_BTN_BLE_ENABLED 1
#endif

// </h>
//==========================================================

// <h> nRF_BLE

//==========================================================
// <q> BLE_ADVERTISING_ENABLED  - ble_advertising - Advertising module


#ifndef BLE_ADVERTISING_ENABLED
#define BLE_ADVERTISING_ENABLED 1
#endif

// <e> NRF_BLE_CONN_PARAMS_ENABLED - ble_conn_params - Initiating and executing a connection parameters negotiation procedure
//==========================================================
#ifndef NRF_BLE_CONN_PARAMS_ENABLED
#define NRF_BLE_CONN_PARAMS_ENABLED 1
#endif
// <o> NRF_BLE_CONN_PARAMS_MAX_SLAVE_LATENCY_DEVIATION - The largest acceptable deviation in slave latency.
// <i> The largest deviation (+ or -) from the requested slave latency that will not be renegotiated.

#ifndef NRF_BLE_CONN_PARAMS_MAX_SLAVE_LATENCY_DEVIATION
#define NRF_BLE_CONN_PARAMS_MAX_SLAVE_LATENCY_DEVIATION 499
#endif

// <o> NRF_BLE_CONN_PARAMS_MAX_SUPERVISION_TIMEOUT_DEVIATION - The largest acceptable deviation (in 10 ms units) in supervision timeout.
// <i> The largest deviation (+ or -, in 10 ms units) from the requested supervision timeout that will not be renegotiated.

#ifndef NRF_BLE_CONN_PARAMS_MAX_SUPERVISION_TIMEOUT_DEVIATION
#define NRF_BLE_CONN_PARAMS_MAX_SUPERVISION_TIMEOUT_DEVIATION 65535
#endif

// </e>

// <q> NRF_BLE_GATT_ENABLED  - nrf_ble_gatt - GATT module


#ifndef NRF_BLE_GATT_ENABLED
#define NRF_BLE_GATT_ENABLED 1
#endif

// <e> NRF_BLE_QWR_ENABLED - nrf_ble_qwr - Queued writes support module (prepare/execute write)
//==========================================================
#ifndef NRF_BLE_QWR_ENABLED
#define NRF_BLE_QWR_ENABLED 1
#endif
// <o> NRF_BLE_QWR_MAX_ATTR - Maximum number of attribute handles that can be registered. This number must be adjusted according to the number of attributes for which Queued Writes will be enabled. If it is zero, the module will reject all Queued Write requests.
#ifndef NRF_BLE_QWR_MAX_ATTR
#define NRF_BLE_QWR_MAX_ATTR 0
#endif

// </e>

// <e> PEER_MANAGER_ENABLED - peer_manager - Peer Manager
//==========================================================
#ifndef PEER_MANAGER_ENABLED
#define PEER_MANAGER_ENABLED 1
#endif
// <o> PM_MAX_REGISTRANTS - Number of event handlers that can be registered.
#ifndef PM_MAX_REGISTRANTS
#define PM_MAX_REGISTRANTS 3
#endif

// <o> PM_FLASH_BUFFERS - Number of internal buffers for flash operations.
// <i> Decrease this value to lower RAM usage.

#ifndef PM_FLASH_BUFFERS
#define PM_FLASH_BUFFERS 4
#endif

// <q> PM_CENTRAL_ENABLED  - Enable/disable central-specific Peer Manager functionality.


// <i> Enable/disable central-specific Peer Manager functionality.

#ifndef PM_CENTRAL_ENABLED
#define PM_CENTRAL_ENABLED 0
#endif

// <q> PM_SERVICE_CHANGED_ENABLED  - Enable/disable the service changed management for GATT server in Peer Manager.


// <i> If not using a GATT server, or using a server wihout a service changed characteristic,
// <i> disable this to save code space.

#ifndef PM_SERVICE_CHANGED_ENABLED
#define PM_SERVICE_CHANGED_ENABLED 1
#endif

// <q> PM_PEER_RANKS_ENABLED  - Enable/disable the peer rank management in Peer Manager.


// <i> Set this to false to save code space if not using the peer rank API.

#ifndef PM_PEER_RANKS_ENABLED
#define PM_PEER_RANKS_ENABLED 1
#endif

// <q> PM_LESC_ENABLED  - Enable/disable LESC support in Peer Manager.


// <i> If set to true, you need to call nrf_ble_lesc_request_handler() in the main loop to respond to LESC-related BLE events. If LESC support is not required, set this to false to save code space.

#ifndef PM_LESC_ENABLED
#define PM_LESC_ENABLED 0
#endif

// <e> PM_RA_PROTECTION_ENABLED - Enable/disable protection against repeated pairing attempts in Peer Manager.
//==========================================================
#ifndef PM_RA_PROTECTION_ENABLED
#define PM_RA_PROTECTION_ENABLED 0
#endif
// <o> PM_RA_PROTECTION_TRACKED_PEERS_NUM - Maximum number of peers whose authorization status can be tracked.
#ifndef PM_RA_PROTECTION_TRACKED_PEERS_NUM
#define PM_RA_PROTECTION_TRACKED_PEERS_NUM 8
#endif
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

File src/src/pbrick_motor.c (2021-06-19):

#include "app_pwm.h"
#include "nrf_gpio.h"
#include "nrf_delay.h"
#include "nrf_log.h"
#include "pbrick_motor.h"
#include "pbrick_board.h"

APP_PWM_INSTANCE(PWM0, 1);

pbrick_motors motors;

/**@brief Ready callback for PWM
 *
 * @param[in] pwm_id    The PWM id
 *
 * @return      void
 */
static void pwm_ready_callback(uint32_t pwm_id)
{
}

/**@brief Setups a motor
 *
 * @param[in] pins      List of pins associated with the motor
 * @param[in] driver    The PWM driver to use
 * @param[in] id        The motor id used internally
 *
 * @return      void
 */
static void motor_setup(uint8_t pins[2], const app_pwm_t *driver, uint8_t id, uint8_t channel)
{
    struct s_pbrick_motor_state s;

    nrf_gpio_cfg_output(pins[0]);
    nrf_gpio_cfg_output(pins[1]);

    memcpy(s.pins, pins, 2);
    s.direction = 1;
    s.pwm = 0;
    s.driver = driver;
    s.id = id;
    s.channel = channel;

    motors.motors[motors.elements] = s;
    motors.elements += 1;
}

/**@brief Setups a 3 wire configuration (PWM, IN0, IN1) for TB6612FNG or similar ICs
 *        The IN0 and IN1 are high/low, and PWM carries the PWM signal to the motor controller
 *
 * @return      void
 */
static void setup()
{
#if defined(PBRICK_PWM0_P1) && defined(PBRICK_PWM0_P2) && defined(PBRICK_PWM0_PWM)
    // If PWM0_P1 and PWM0_P2 are defined, setup that motor group
    uint8_t motor_pins[2] = { PBRICK_PWM0_P1, PBRICK_PWM0_P2 };
    motor_setup(motor_pins, &PWM0, 1, 0);
#endif

#if defined(PBRICK_PWM1_P1) && defined(PBRICK_PWM1_P2) && defined(PBRICK_PWM1_PWM)
    // If PWM1_P1 and PWM1_P2 are defined, setup that motor group
    uint8_t motor_pins2[2] = { PBRICK_PWM1_P1, PBRICK_PWM1_P2 };
    motor_setup(motor_pins2, &PWM0, 2, 1);
#endif

#if defined(PBRICK_PWM0_PWM) && defined(PBRICK_PWM1_PWM)
    // If PWM0_P1 and PWM0_P2 and PWM1_P1 and PWM1_P2 are setup, create a dual channel PWM config
    app_pwm_config_t pwm_cfg = APP_PWM_DEFAULT_CONFIG_2CH(5000L, PBRICK_PWM0_PWM, PBRICK_PWM1_PWM);
    pwm_cfg.pin_polarity[0] = APP_PWM_POLARITY_ACTIVE_HIGH;
    pwm_cfg.pin_polarity[1] = APP_PWM_POLARITY_ACTIVE_HIGH;
#else
    // If PWM0_P1 and PWM0_P2 are the only pins setup, create a single channel PWM config
    app_pwm_config_t pwm_cfg = APP_PWM_DEFAULT_CONFIG_1CH(5000L, PBRICK_PWM0_PWM);
    pwm_cfg.pin_polarity[0] = APP_PWM_POLARITY_ACTIVE_HIGH;
#endif

    ret_code_t err_code = app_pwm_init(&PWM0, &pwm_cfg, pwm_ready_callback);
    APP_ERROR_CHECK(err_code);
    app_pwm_enable(&PWM0);
}

ret_code_t pbrick_motor_init()
{
    // Create mock sentinel values.
    motors.size = 2;
    motors.elements = 0;

    for (int i = 0; i < motors.size; i++) {
        motors.motors[i].id = -1;
    }

    setup();

    return NRF_SUCCESS;
}

ret_code_t pbrick_motor_enable()
{
    return NRF_SUCCESS;
}

ret_code_t pbrick_motor_disable()
{
    return NRF_SUCCESS;
}

void pbrick_motor_set_internal(uint8_t motor, uint8_t direction, uint8_t pwm)
{

    motors.motors[motor].direction = direction;
    motors.motors[motor].pwm = pwm;
    uint8_t channel = motors.motors[motor].channel;
    uint8_t motorId = motors.motors[motor].id;

    const app_pwm_t *driver = motors.motors[motor].driver;

    int speed = (int)pwm;
    if (speed > 100) {
        NRF_LOG_INFO("Adjusting speed %x in excess to 100", speed)
        speed = 100;
    }

    while (app_pwm_channel_duty_set(driver, channel, abs(motors.motors[motor].pwm)) == NRF_ERROR_BUSY);

    if (direction == 0x00) {
        nrf_gpio_pin_clear(motors.motors[motor].pins[0]);
        nrf_gpio_pin_set(motors.motors[motor].pins[1]);
    } else if (direction == 0x01) {
        nrf_gpio_pin_clear(motors.motors[motor].pins[1]);
        nrf_gpio_pin_set(motors.motors[motor].pins[0]);
    } else {
        NRF_LOG_WARNING("%X motor direction is not defined", direction);
    }

    NRF_LOG_DEBUG("Set Motor %d: Direction: %X Speed: %X", motorId, direction, speed);
}


ret_code_t pbrick_motor_set(const uint8_t data[])
{
    uint8_t motor = data[0];
    uint8_t pwm = data[1];
    uint8_t direction = data[2];

    // For PWM0, set the channel and speed directly since PWM just controls the speed
    if (motor == 0x00 || motor == 0x01) {
        pbrick_motor_set_internal(motor, direction, pwm);
    } else {
#if defined(PBRICK_PWM0_PWM) && defined(PBRICK_PWM1_PWM)
        // Motor startup needs to be in sync - stoping all motors then disabling PWM
        pbrick_motor_stop_all();

        if (motor == 0x02) {
            // Set both motors to operate in the same rotational direction
            pbrick_motor_set_internal(0x00, direction, pwm);
            pbrick_motor_set_internal(0x01, direction, pwm);
        } else if (motor == 0x03) {
            // Set both motors to operate in opposite directions
            pbrick_motor_set_internal(0x00, direction, pwm);
            pbrick_motor_set_internal(0x01, (direction ^ 0x01), pwm);
        } else {
            NRF_LOG_WARNING("Motor Option (%X) is not defined", motor);
        }
#else
        NRF_LOG_WARNING("Dual channel motor not setup. Unable to set.")
#endif
    }

    return NRF_SUCCESS;
}

void pbrick_motor_stop(uint8_t motor)
{
    uint8_t motorId = motors.motors[motor].id;
    if (motorId == -1) {
        NRF_LOG_INFO("Unable to force stop motor due to undefined instance.");
        return;
    } else {
        NRF_LOG_INFO("Force stopping motor %d", motorId);
    }

    nrf_gpio_pin_clear(motors.motors[motor].pins[0]);
    nrf_gpio_pin_clear(motors.motors[motor].pins[1]);

    pbrick_motor_set_internal(motor, 0x00, 0x00);
}

void pbrick_motor_stop_all()
{
    for (int i = 0; i < motors.size; i++) {
        uint8_t motorId = motors.motors[i].id;
        if (motorId != -1) {
            pbrick_motor_stop(motorId);
        }
    }
}

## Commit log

2020-12-21 Merging board source code with firmware
    [pbrick.kicad_pcb, pbrick.sch]
2020-12-31 Converting to 24mm x 45mm board
    [pbrick.kicad_pcb, pbrick.sch]
2021-01-23 Updating board bSilk, pin definitions
    [pbrick.kicad_pcb]
2021-01-23 Updating board
    [pbrick.kicad_pcb]
2021-01-31 Type-C built-in power
    [pbrick.kicad_pcb, pbrick.sch]
2021-01-31 USB-PD Type-C Support
    [pbrick.kicad_pcb, pbrick.sch]
2021-02-01 Updating 3D model
    [pbrick.kicad_pcb]
2021-02-02 Adding new symbols
    [pbrick.sch]
2021-02-02 TD2030 pin connector instead of CotexDebug, routable path
    [pbrick.kicad_pcb, pbrick.sch]
2021-02-02 New board fill
    [pbrick.kicad_pcb]
2021-02-03 Starting work on STUSB4500 USB i2C connection for new board design
    [pbrick.kicad_pcb, pbrick.sch]
2021-02-04 Initialize TWI - Currently stuck on nrf_drv_twi_tx #78 not executing completing in async mode
    [main.c]
2021-02-04 TWI in blocking model successfully initializes STUSB4500 - @todo: Implement 9V2A switch and verify PDO output
2021-02-07 Working STUSB4500 i2c interface
2021-02-07 Fixing router keepout zone issue with vias
    [pbrick.kicad_pcb]
2021-02-22 Added 3-axis sensor Added dedicate PWM driver Added 2 MOLEX connectors 3x5 (24mm x 40mm)
    [pbrick.kicad_pcb, pbrick.sch]
2021-02-23 Updating footprints
    [pbrick.kicad_pcb, pbrick.sch]
2021-02-23 Updating parts list
    [pbrick.sch]
2021-02-23 Minor part update
    [pbrick.kicad_pcb]
2021-03-07 Adding BOM information for PCA9632BS
    [pbrick.sch]
2021-03-07 Fixes design defect with 0402 resistor pads Adds NXP LED driver DigiKey Part information for ordering Adds more space for SWD connector Spaces out QWIIC and USB-C connector
    [pbrick.kicad_pcb, pbrick.sch]
2021-03-08 Correct schematic defect where Q2 was not routed on both ends
    [pbrick.kicad_pcb, pbrick.sch]
2021-03-11 5v regulator has operational capacity from 2.7-20v (tested) - removing extra diode and 2.7v line as 5v => 3.3v works at 5v input
    [pbrick.kicad_pcb, pbrick.sch]
2021-03-11 Updating PCB routing
    [pbrick.kicad_pcb]
2021-03-11 Updating PCB layout
    [pbrick.kicad_pcb]
2021-03-22 Updating PCB to resolve an issue with PCA9624 OE being HIGH instead of Controller - Added PCA9624 library definition (untested) - Convert pbrick_motor to use PCA9624 driver
    [pbrick.kicad_pcb, pbrick.sch]
2021-03-28 Updating layout
    [pbrick.kicad_pcb, pbrick.sch]
2021-03-28 Updating board, definitions
    [pbrick.kicad_pcb]
2021-03-28 Updating PCB
    [pbrick.kicad_pcb]
2021-03-30 Updating part list. Missing alt 12v connector
    [pbrick.kicad_pcb, pbrick.sch]
2021-03-31 Adding extra vin, manual routing
    [pbrick.kicad_pcb, pbrick.sch]
2021-04-01 Unfillfing zones
    [pbrick.kicad_pcb]
2021-04-01 New routing
    [pbrick.kicad_pcb]
2021-04-01 Updating Board, schematic, generated files
    [pbrick.kicad_pcb, pbrick.sch]
2021-04-02 Minor board layout update
    [pbrick.kicad_pcb]
2021-04-18 PCA9642 nonfunctional on board
2021-04-27 PCA9624 still doesn't work
    [pbrick_board.h, pbrick_motor.c]
2021-06-03 Reverting to APP_PWM from board
    [pbrick.kicad_pcb, pbrick.sch]
2021-06-19 Wrong board wiring again...
    [pbrick.kicad_pcb, pbrick.sch]
2021-06-20 Minor board update
    [pbrick.kicad_pcb, pbrick.sch]
2021-06-20 Minor wire change
    [pbrick.kicad_pcb]
2021-07-11 Updating Board layout, pcb, board definition
    [pbrick.kicad_pcb, pbrick.sch]
2021-12-03 Updating board layout to align with other PF modules - Swapped GND and VDD on M0 and M0 to avoid wire crossing in cable wiring (external) - Swapped M1_0 and M1_1 to eliminate trace crossover (will so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
    [pbrick.kicad_pcb, pbrick.sch]

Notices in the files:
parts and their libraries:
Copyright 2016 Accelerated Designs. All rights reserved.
